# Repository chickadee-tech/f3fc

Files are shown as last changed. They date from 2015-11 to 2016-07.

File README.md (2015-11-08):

# Chickadee Tech F3FC #
This an STM32F3-based flight control Polystack board for multirotors designed by Chickadee Tech. It features an STM32F303VCT6 microcontroller and an MPU-6000 accelerometer/gyroscope. It runs a modified version of [Betaflight]() available [here](github.com/chickadee-tech/betaflight) with the CKD_F3FC target.

## Documentation ##
See the [wiki](https://github.com/chickadee-tech/f3fc/wiki) for documentation.

## Polystack ##
This **control** board is part of the Polystack platform for modular microcontrol systems. More information on the platform can be found at [polystack.org](http://polystack.org).

## Support ##
If you need support with a board you own or have development questions please email support@chickadee.tech or check chickadee.tech/support for other ways to get support.

## Support ##
If you need support with a board you own or have development questions please email support@chickadee.tech or check [chickadee.tech/support](https://chickadee.tech/support) for other ways to get support.

## Contributing ##
Please note that this project is released with a [Contributor Code of Conduct](CODE_OF_CONDUCT.md). By participating in this project you agree to abide by its terms.

### Setup ###
Components and footprints for PCB parts are not included in this repository. Instead, checkout the [chickadee-tech/kicad-libs](https://github.com/chickadee-tech/kicad-libs) repository in the same directory that this repository is checked out in. All part definitions should be relative so that they will load correctly.

### Pull requests ###
For fixes please submit a pull request to the original repository. After the pull request is merged, check the [Chickadee Tech Active Contributor Discount (ACD)](https://chickadee.tech/active-contributor) to see if you are eligible for a discount code to use on your next purchase.

### Derivatives ###
If developing your own version of the F3FC board please remove all Chickadee Tech trademarks and follow the [CC-BY license](LICENSE). While not required, please consider open sourcing your modifications so others can learn from your improvements. If you do email support@chickadee.tech and we may choose to add your project to the ACD.

You may also license the Polystack logo for free by emailing support@chickadee.tech. We'll ask for your gerbers to ensure the design complies with specifications laid out [here](https://github.com/chickadee-tech/polystack/wiki) and provide written permission to use the trademark after compliance has been demonstrated.

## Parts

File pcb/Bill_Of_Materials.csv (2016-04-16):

part name | symbol | size (imp) | max current | unit price | units per build | units in stock | On Order | order total | Manufacturer ID | digikey url | Mouser | MacroFab HP | datasheet | datasheet2
C 10nF (0.01uF, 10000pF) X7R | C5 | 603 |  | $0.01 | 1 | 96 | SMD Binder - Capacitors | $0.01 | 06035C103KAT2A | http://www.digikey.com/product-detail/en/06035C103KAT2A/478-1227-1-ND/564259 |  | Y | http://datasheets.avx.com/X7RDielectric.pdf
C 10uF X5R | C11 | 1206 |  | $0.24 | 1 | 80 | SMD Binder - Capacitors | $0.24 | C3216X5R1C106M160AA | http://www.digikey.com/product-detail/en/C3216X5R1C106M160AA/445-1426-1-ND/569092 |  | MF-CAP-1206-10uF | http://product.tdk.com/en/catalog/datasheets/mlcc_commercial_general_en.pdf
C 1uF X7R | C12 | 603 |  | $0.03 | 1 | 20 | SMD Binder - Capacitors | $0.03 | TMK107B7105KA-T | http://www.digikey.com/product-detail/en/TMK107B7105KA-T/587-2984-1-ND/2714177 |  | MF-CAP-0603-1uF | http://ds.yuden.co.jp/TYCOMPAS/ut/detail.do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
C 2.2nF (2200pF) X7R 50V | C1 | 603 |  | $0.01 | 1 | 94 | SMD Binder - Capacitors | $0.01 | C0603C222K5RACTU | http://www.digikey.com/product-detail/en/C0603C222K5RACTU/399-1085-1-ND/411360 | http://www.mouser.com/ProductDetail/Kemet/C0603C222K5RACTU/?qs=sGAEpiMZZMs0AnBnWHyRQFqPnX0OlvcoEeor2YsHDUE%3d | N
C 2.2uF | C14, C15 | 603 |  | $0.05 | 2 | 92 | SMD Binder - Capacitors | $0.09 | C0603C225K9PACTU | http://www.digikey.com/product-detail/en/C0603C225K9PACTU/399-3362-1-ND/650351 | http://www.mouser.com/ProductDetail/Kemet/C0603C225K9PACTU/?qs=sGAEpiMZZMs0AnBnWHyRQJIiGvDVk92V8FIBbbmgLZk%3d
C 0.1uF | C2, C3, C7, C8, C9, C10, C13 | 603 |  | $0.02 | 7 | 400 | SMD Binder - Capacitors | $0.15 | C0603C104K4RACTU | http://www.digikey.com/product-detail/en/C0603C104K4RACTU/399-1096-1-ND/411371 |  | MF-CAP-0603-0.1uF | http://www.kemet.com/docfinder?Partnumber=C0603C104K4RACTU
red led | D3,D5 |  |  | $0.19 | 2 | 71 | SMD Binder - Diodes | $0.37 | LTST-C190KRKT | http://www.digikey.com/product-detail/en/LTST-C190KRKT/160-1436-1-ND/386816 |  | MF-LED-0603-RED | http://optoelectronics.liteon.com/upload/download/DS-22-99-0151/S_110_LTST-C190KRKT.pdf
green led | D1 |  |  | $0.19 | 1 | 83 | SMD Binder - Diodes | $0.19 | LTST-C190KGKT | http://www.digikey.com/product-detail/en/LTST-C190KGKT/160-1435-1-ND/386814 |  | Y | http://optoelectronics.liteon.com/upload/download/DS22-2000-074/S_110_LTST-C190KGKT.pdf
yellow led | D2 |  |  | $0.20 | 1 | 87 | SMD Binder - Diodes | $0.20 | LTST-C190KSKT | http://www.digikey.com/product-detail/en/LTST-C190KSKT/160-1437-1-ND/386818 |  | N | http://optoelectronics.liteon.com/upload/download/DS-22-99-0189/S_110_LTST-C190KSKT.pdf
Power OR Diode | D4 |  | 500mA | $0.49 | 1 | 6 | SMD Binder - Diodes | $0.49 | PMEG2005CT,215 | http://www.digikey.com/product-detail/en/PMEG2005CT,215/568-6500-1-ND/2531787 | http://www.mouser.com/ProductDetail/NXP/PMEG2005CT215/ | N | http://www.nxp.com/documents/data_sheet/PMEG2005CT.pdf
~3.5mm Spacer | Off Board |  |  | $0.08 | 5 | 81 | SMD Binder - Connectors | $0.42 | 908-140 | http://www.mouser.com/search/ProductDetail.aspx?R=0virtualkey0virtualkey908-140 |  | N
Nylon Hex Nut | Off Board |  |  | $0.10 | 9 | 94 | SMD Binder - Connectors | $0.86 | 4688 | http://www.mouser.com/ProductDetail/Keystone-Electronics/4688/ |  | N
1x2 housing | Off Board |  |  | $0.08 | 4 | 48 | SMD Binder - Connectors | $0.31 | M20-1060200 | http://www.digikey.com/product-detail/en/M20-1060200/952-2227-ND/3728191 | http://www.mouser.com/ProductDetail/Harwin/M20-1060200/ | N
usb otg | P2 |  | 500mA | $0.46 | 1 | 7 | SMD Binder - Connectors | $0.46 | 10118193-0001LF | http://www.digikey.com/product-detail/en/10118193-0001LF/609-4616-1-ND/2785380 | http://www.mouser.com/ProductDetail/FCI/10118193-0001LF/ | MF-CON-MICROUSB-RIGHT | http://portal.fciconnect.com/Comergent//fci/drawing/10118193.pdf
80 pin receptacle (3.5mm) | P4 |  | 0.3A a pin | $2.42 | 1 | 1 | SMD Binder - Connectors | $2.42 | DF40HC(3.5)-80DS-0.4V(51) | http://www.digikey.com/product-detail/en/DF40HC(3.5)-80DS-0.4V(51)/H11997CT-ND/2880228 | http://www.mouser.com/ProductDetail/Hirose-Electric/DF40HC35-80DS-04V51/ | N | http://www.hirose.co.jp/cataloge_hp/ed_DF40_20140305.pdf
20pin hirose header | P5 |  | 0.3A a pin | $0.79 | 1 | 7 | SMD Binder - Connectors | $0.79 | DF40C-20DP-0.4V(51) | http://www.digikey.com/product-detail/en/DF40C-20DP-0.4V(51)/H11618CT-ND/1969498 | http://www.mouser.com/ProductDetail/Hirose-Electric/DF40C-20DP-04V51/ | N | http://www.hirose.co.jp/cataloge_hp/ed_DF40_20140305.pdf
Chickadee F3FC v7 | PCB |  |  | $6.73 | 1 | 3 |  | $6.73 | CKD-F3FC-V7 |  |  | N
p-channel mosfet | Q1 | TO-236-3, SC-59, SOT-23-4 | 220mA continuous | $0.10 | 1 | 97 | SMD Binder - ICs | $0.10 | BSS84 | http://www.digikey.com/product-detail/en/fairchild-semiconductor/BSS84/BSS84CT-ND/244297 | http://www.mouser.com/search/ProductDetail.aspx?R=0virtualkey0virtualkeyBSS84 | MF-DSC-SOT233-BSS84 | https://www.fairchildsemi.com/datasheets/BS/BSS84.pdf
n-channel mosfet | Q3, Q4 | TO-236-3, SC-59, SOT-23-3 | 220mA continuous | $0.09 | 2 | 59 | SMD Binder - ICs | $0.19 | BSS138 | http://www.digikey.com/product-detail/en/BSS138/BSS138CT-ND/244294 |  | MF-DSC-SOT233-BSS138 | https://www.fairchildsemi.com/datasheets/BS/BSS138.pdf
R 1k | R1, R2, R3, R12 | 603 |  | $0.01 | 4 | 993 | SMD Binder - Resistors | $0.04 | RC0603FR-071KL | http://www.digikey.com/product-detail/en/RC0603FR-071KL/311-1.00KHRCT-ND/729790 |  | MF-RES-0603-1K | http://www.yageo.com/NewPortal/yageodocoutput?fileName=/pdf/R-Chip/PYu-RC_Group_51_RoHS_L_3.pdf
R 4.7k | R4, R11 | 1206 |  | $0.01 | 2 | 68 | SMD Binder - Resistors | $0.01 | RC0603FR-074K7L | http://www.digikey.com/product-detail/en/RC0603FR-074K7L/311-4.70KHRCT-ND/730159 |  | MF-RES-0603-5.6K | http://www.yageo.com/NewPortal/yageodocoutput?fileName=/pdf/R-Chip/PYu-RC_Group_51_RoHS_L_3.pdf
R 10k | R5, R7 | 603 |  | $0.01 | 2 | 979 | SMD Binder - Resistors | $0.02 | RC0603FR-0710KL | http://www.digikey.com/product-detail/en/RC0603FR-0710KL/311-10.0KHRCT-ND/729827 |  | MF-RES-0603-10K | http://www.yageo.com/NewPortal/yageodocoutput?fileName=/pdf/R-Chip/PYu-RC_Group_51_RoHS_L_3.pdf
R 1.5k | R6 | 603 |  | $0.01 | 1 | 0 |  | $0.01 | RC0603FR-071K5L | http://www.digikey.com/product-detail/en/yageo/RC0603FR-071K5L/311-1.50KHRCT-ND/729811 |  | N
R 100k | R10 | 603 |  | $0.01 | 1 | 55 | SMD Binder - Resistors | $0.01 | RC0603FR-07100KL | http://www.digikey.com/product-detail/en/RC0603FR-07100KL/311-100KHRCT-ND/729836 |  | MF-RES-0603-100K | http://www.yageo.com/NewPortal/yageodocoutput?fileName=/pdf/R-Chip/PYu-RC_Group_51_RoHS_L_3.pdf
R 470k | R9 | 603 |  | $0.01 | 1 | 68 | SMD Binder - Resistors | $0.01 | RC0603FR-07470KL | http://www.digikey.com/product-detail/en/RC0603FR-07470KL/311-470KHRCT-ND/730204 |  | MF-RES-0603-470K | http://www.yageo.com/NewPortal/yageodocoutput?fileName=/pdf/R-Chip/PYu-RC_Group_51_RoHS_L_3.pdf
reset- side switch | SW1 | EVQ-P7A |  | $0.69 | 1 | 7 | SMD Binder - Misc | $0.69 | EVQ-P7A01P | http://www.digikey.com/product-detail/en/EVQ-P7A01P/P16763CT-ND/4429456 | http://www.mouser.com/ProductDetail/Panasonic/EVQ-P7A01P/ | N | http://media.digikey.com/pdf/Data%20Sheets/Panasonic%20Electronic%20Components/EVQP(7,3,9P7).pdf
acc/gyro | U1 | 24pin QFN 4x4 |  | $10.72 | 1 | 4 | SMD Binder - ICs | $10.72 | MPU-6000 | http://www.digikey.com/product-detail/en/MPU-6000/1428-1005-1-ND/4038006 |  | N | http://store.invensense.com/datasheets/invensense/MPU-6050_DataSheet_V3%204.pdf
STM32F303 | U2 | LQFP-100 | 160mA | $8.66 | 1 | 3 | SMD Binder - ICs | $8.66 | STM32F303VCT6- | http://www.digikey.com/product-detail/en/STM32F303VCT6/497-13233-ND/3598127 | http://www.mouser.com/ProductDetail/STMicroelectronics/STM32F303VCT6/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 | N | http://www.st.com/st-web-ui/static/active/en/resource/technical/document/datasheet/DM00058181.pdf | Total Price | $36.32
3.3v regulator | U3 | SOT23-5 | 0.3A | $0.49 | 1 | 8 | SMD Binder - ICs | $0.49 | TLV70233DBVR | http://www.digikey.com/product-detail/en/TLV70233DBVR/296-32415-1-ND/3505572 | http://www.mouser.com/ProductDetail/Texas-Instruments/TLV70233DBVR/?qs=sGAEpiMZZMu%2feW%252ba9Wiy7YTpE8hEJFai | MF-REG-SOT235-3.3V-300mA | http://www.ti.com/lit/ds/symlink/tlv702.pdf
8mhz resonator | X1 |  |  | $0.38 | 1 | 8 | SMD Binder - Misc | $0.38 | CSTCE8M00G55-R0 | https://www.digikey.com/product-detail/en/CSTCE8M00G55-R0/490-1195-1-ND/584632 | http://www.mouser.com/ProductDetail/Murata/CSTCE8M00G55-R0/ | N | http://www.murata.com/~/media/webrenewal/support/library/catalog/products/timingdevice/ceralock/p16e.ashx
2x4 right angle | Off Board |  |  | $0.80 | 1 | 2 | SMD Binder - Connectors | $0.80 | 5-102975-4 |  | http://www.mouser.com/ProductDetail/TE-Connectivity-AMP/5-102975-4/ | N
~2mm Spacer | Off Board |  |  | $0.08 | 5 | 100 | SMD Binder - Connectors | $0.42 | 908-080 | http://www.mouser.com/ProductDetail/Bivar/908-080/?qs=sGAEpiMZZMtU66%252bVMtdfbpPy1E%252bha670 |  | N | http://www.bivar.com/Portals/0/Products/d.ashx?f=/Portals/0/products/9XX-XXX.pdf

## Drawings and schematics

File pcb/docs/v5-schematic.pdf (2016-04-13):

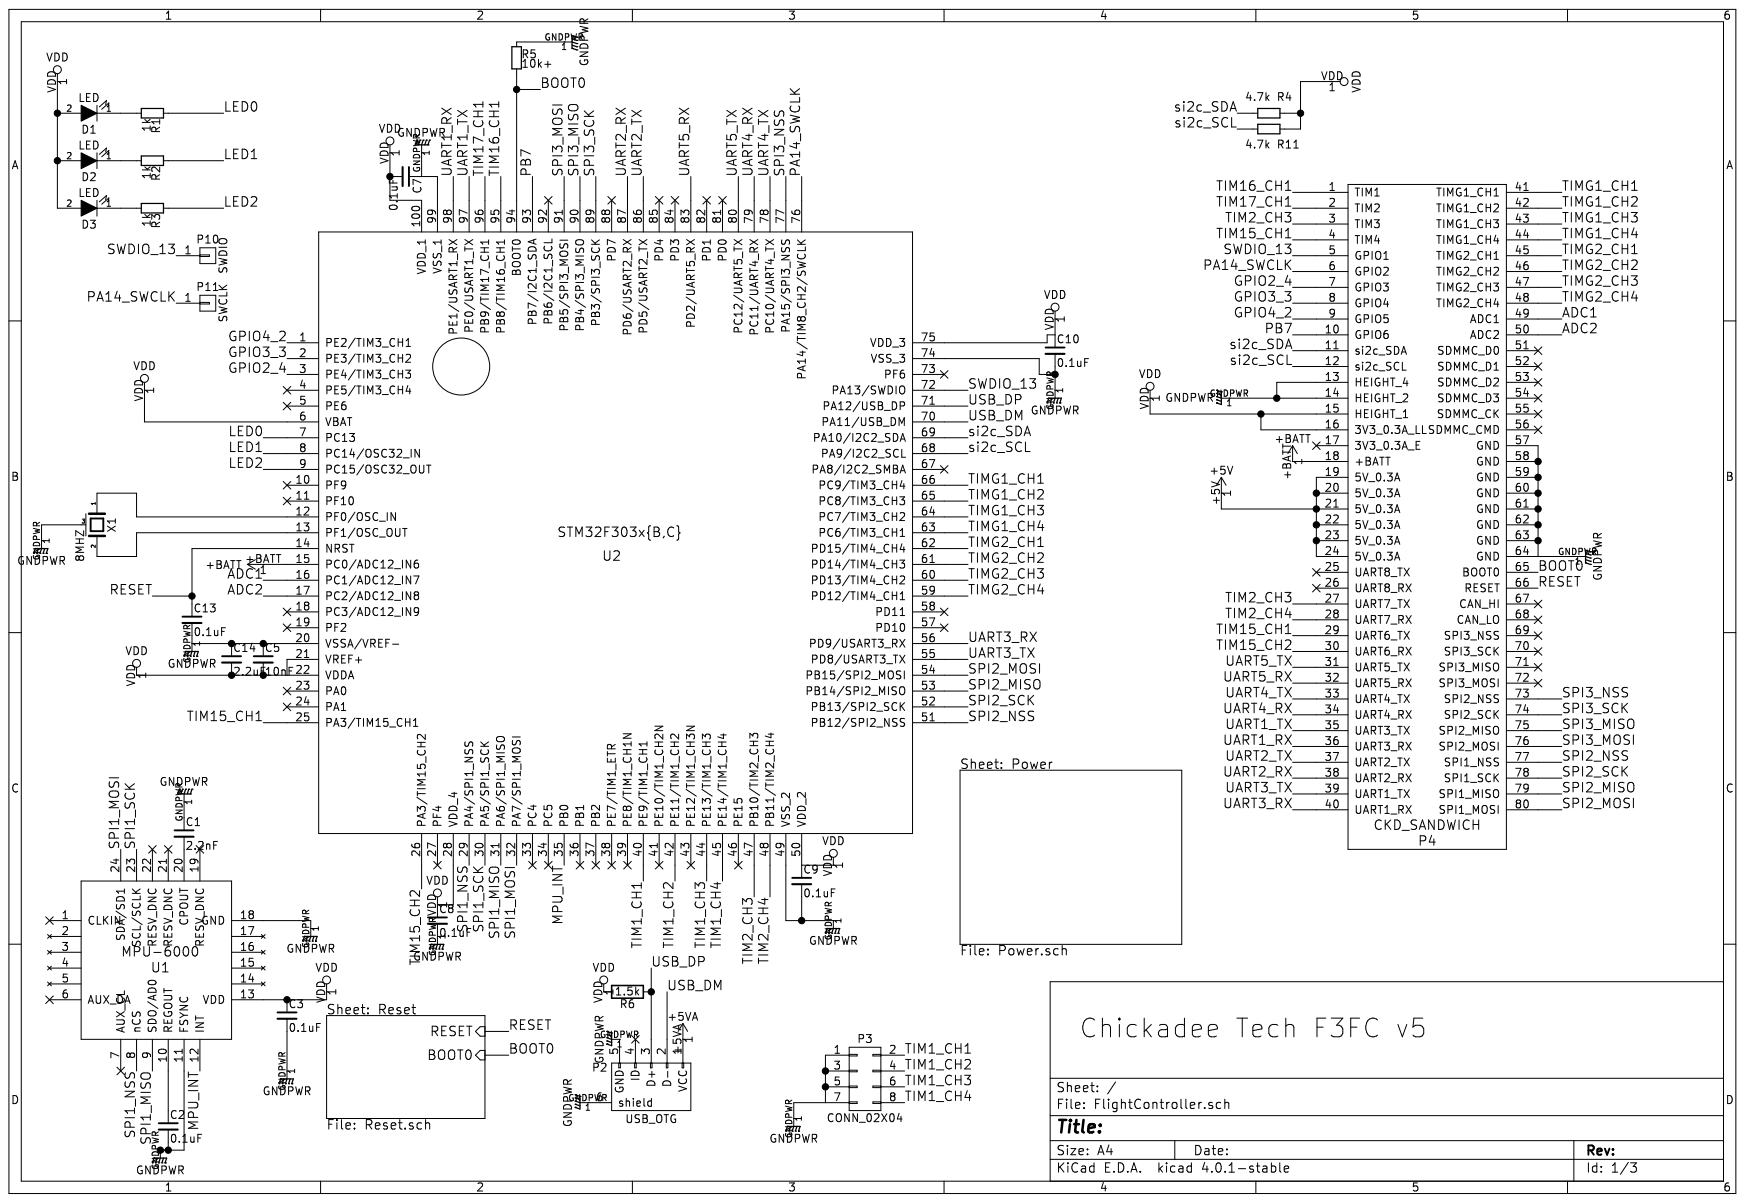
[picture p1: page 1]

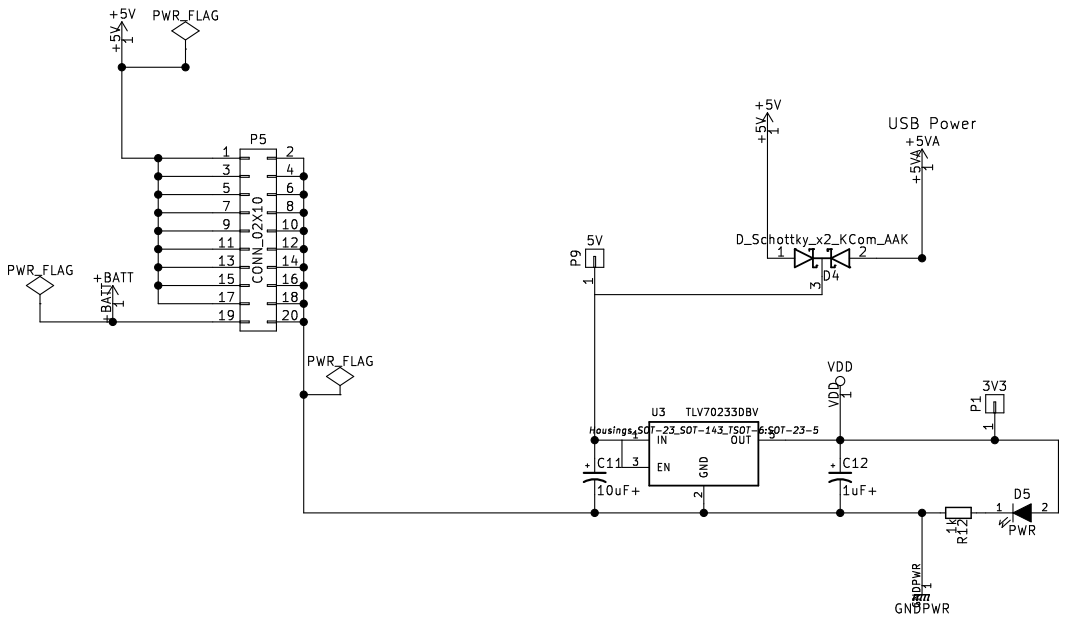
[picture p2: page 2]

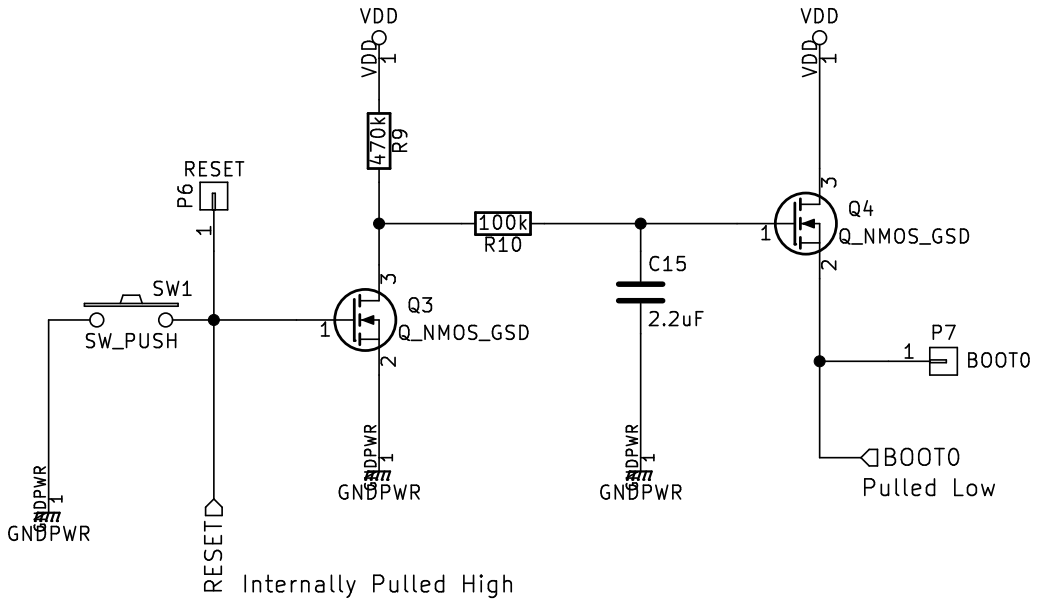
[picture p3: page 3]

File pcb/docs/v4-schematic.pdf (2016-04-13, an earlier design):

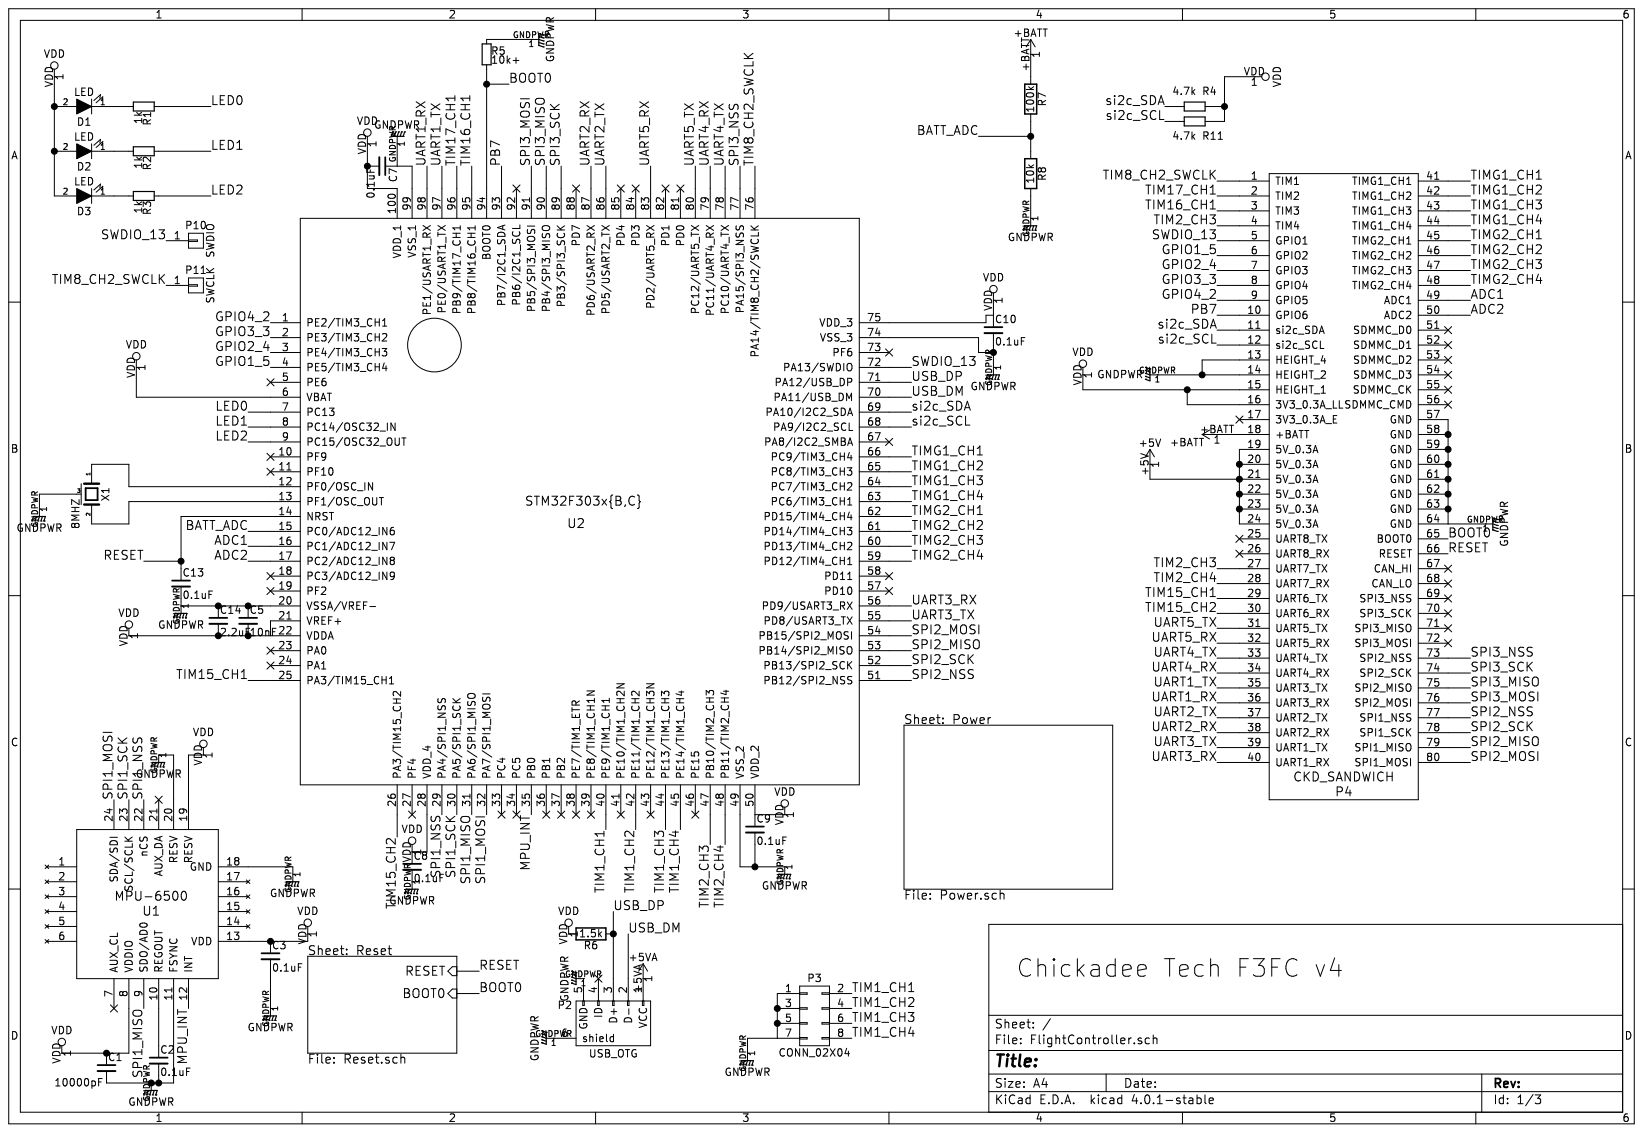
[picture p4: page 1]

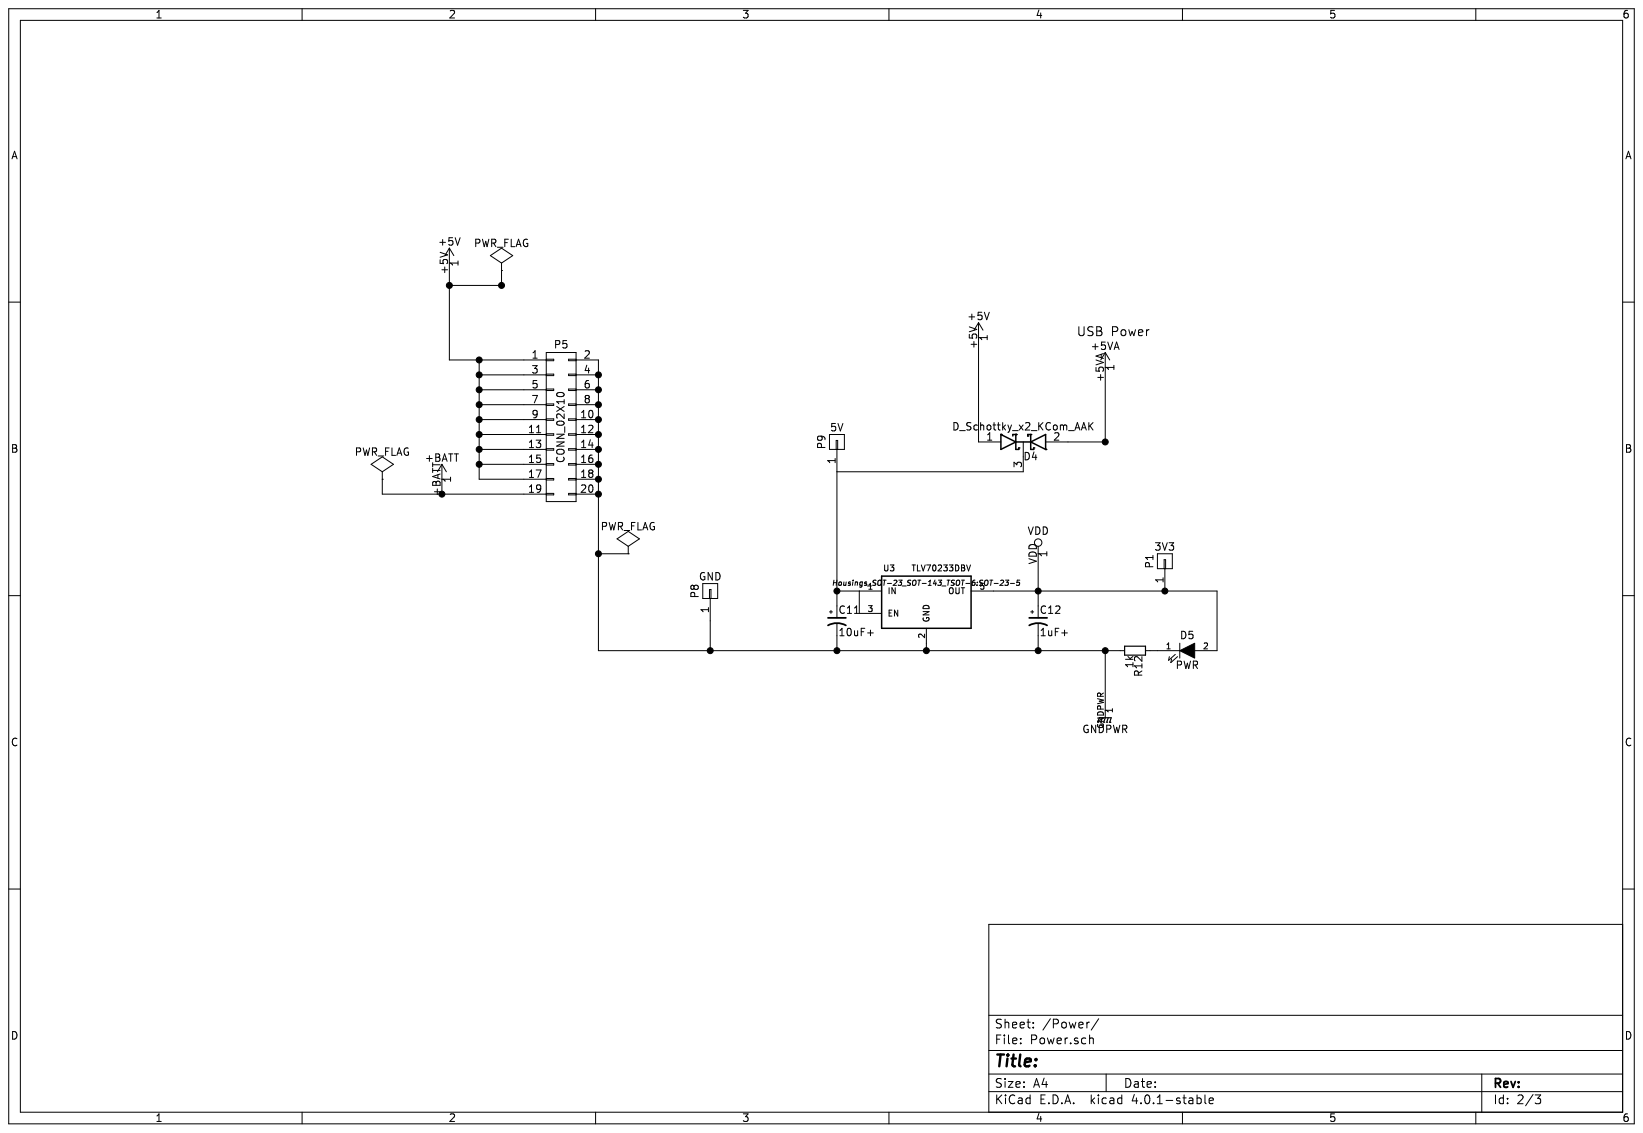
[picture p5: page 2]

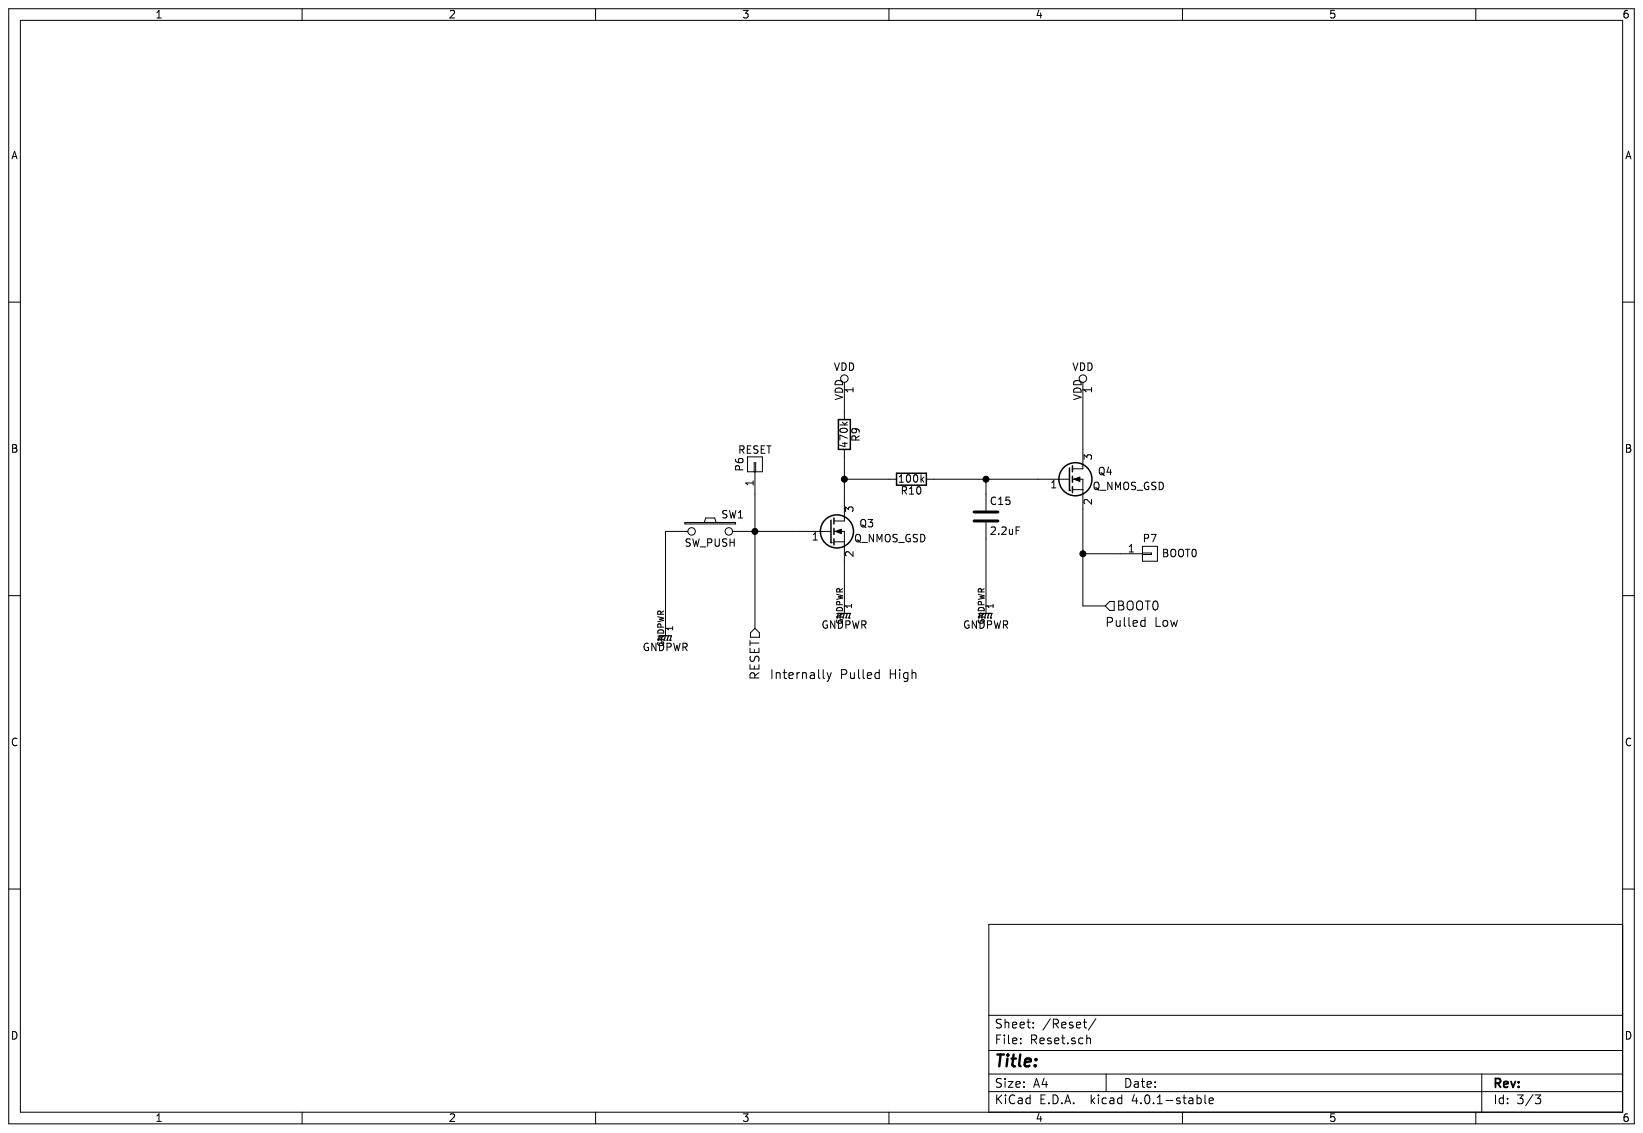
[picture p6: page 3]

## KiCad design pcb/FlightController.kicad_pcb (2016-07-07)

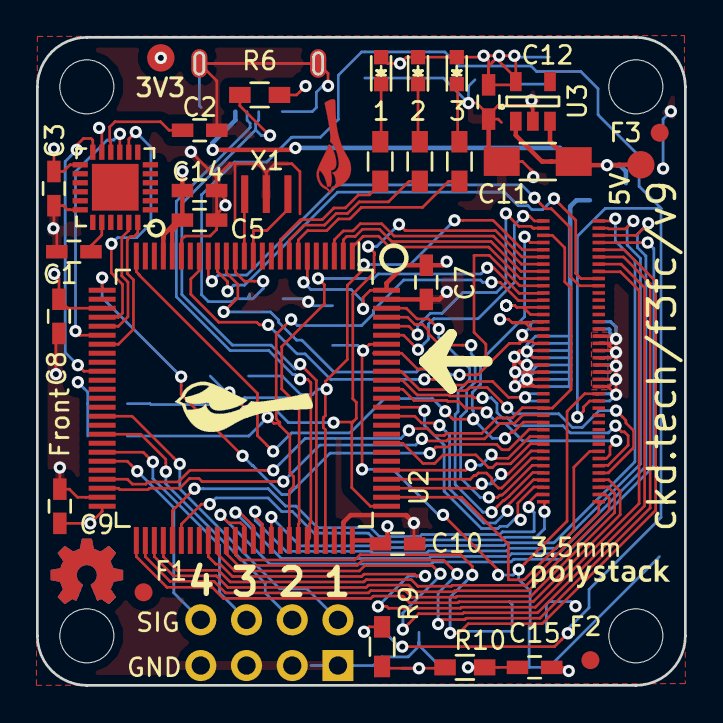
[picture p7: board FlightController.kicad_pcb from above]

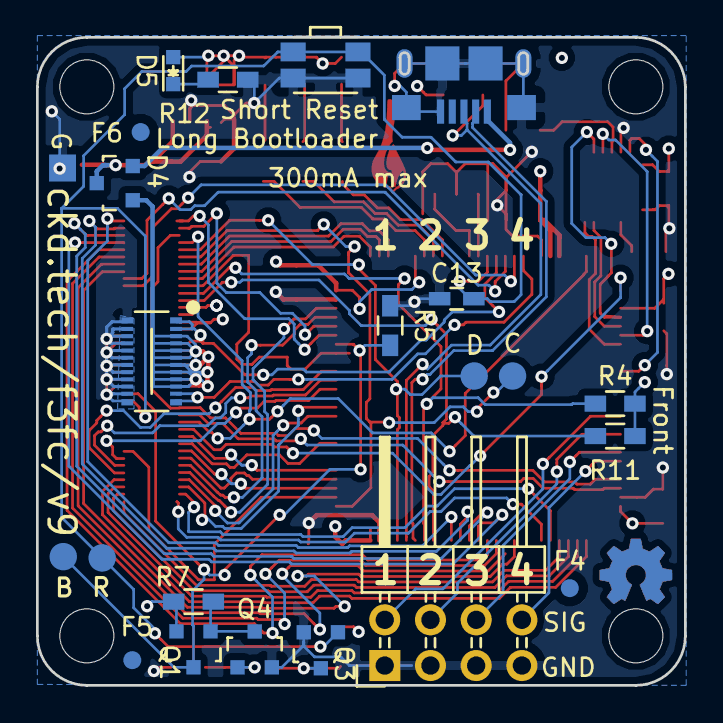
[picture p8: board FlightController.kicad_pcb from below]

Board: 4 copper layers, 36.0 x 36.0 mm, 55 parts (23 on the bottom side), 76 nets.

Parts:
C1: 2.2nF; C_0603_HandSoldering
C2, C3, C7, C8, C9, C10, C13: 0.1uF; C_0603_HandSoldering
C5: 10nF; C_0603_HandSoldering
C11: 10uF+; C_1206_HandSoldering
C12: 1uF+; C_0603_HandSoldering
C14, C15: 2.2uF; C_0603_HandSoldering
D1: Green; LED-0603
D2: Yellow; LED-0603
D3, D5: Red; LED-0603
D4: D_Schottky_x2_KCom_AAK; SOT-23
F1, F2, F3, F4, F5, F6: 1mm; Fiducial
P1: 3V3; Measurement_Point_Round-SMD-Pad_Small
P2: USB_OTG; Mini-USB-B-EDGE
P3: CONN_02X04; Pin_Header_Angled_2x04
P4: CKD_SANDWICH; DF40-3-4mm-80pin-Receptacle
P5: CONN_02X10; DF40-20pin-Header
P6: RESET; Measurement_Point_Round-SMD-Pad_Small
P7: BOOT0; Measurement_Point_Round-SMD-Pad_Small
P8: CONN_01X01; Measurement_Point_Square-SMD-Pad_Small
P9: 5V; Measurement_Point_Round-SMD-Pad_Small
P10: SWDIO; Measurement_Point_Round-SMD-Pad_Small
P11: SWCLK; Measurement_Point_Round-SMD-Pad_Small
Q1: Q_PMOS_GSD; SOT-23
Q3, Q4: Q_NMOS_GSD; SOT-23
R1, R2, R3, R12: 1k; R_0603_HandSoldering
R4, R11: 4.7k; R_0603_HandSoldering
R5: 10k+; R_0603_HandSoldering
R6: 1.5k; R_0603_HandSoldering
R7: 10k; R_0603_HandSoldering
R9: 470k; R_0603_HandSoldering
R10: 100k; R_0603_HandSoldering
SW1: SW_PUSH; SW_SPST_EVQP7A
U1: MPU-6000; QFN-24-1EP_4x4mm_Pitch0.5mm
U2: STM32F303x{B,C}; LQFP-100_14x14mm_Pitch0.5mm
U3: TLV70233DBV; SOT-23-5
X1: 8MHZ; CSTCE_G-CSTCE_G_Z
svg2mod: G***; polystack-bold-0.4

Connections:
+5V: D4.1, P4.19, P4.20, P4.21, P4.22, P4.23, P4.24, P5.3, P5.5, P5.7, P5.9, P5.11, P5.13, P5.15, P5.17
+5VA: D4.2, P2.1
+BATT: P4.18, P5.19, U2.15
/ADC1: P4.49, U2.16
/ADC2: P4.50, U2.17
/GPIO2_4: P4.7, U2.3
/GPIO3_3: P4.8, U2.2
/GPIO4_2: P4.9, U2.1
/LED0: R3.1, U2.7
/LED1: R2.1, U2.8
/LED2: R1.1, U2.9
/MPU_INT: U1.12, U2.35
/PA14_SWCLK: P4.6, P11.1, U2.76
/PB7: P4.10, U2.93
/Power/CURRENT: P5.1, U2.18
/Reset/BOOT0: P4.65, P7.1, Q1.3, R5.2, U2.94
/Reset/RESET: C13.1, P4.66, P6.1, Q3.1, SW1.2, U2.14
/SPI1_MISO: U1.9, U2.31
/SPI1_MOSI: U1.24, U2.32
/SPI1_NSS: U1.8, U2.29
/SPI1_SCK: U1.23, U2.30
/SPI2_MISO: P4.79, U2.53
/SPI2_MOSI: P4.80, U2.54
/SPI2_NSS: P4.77, U2.51
/SPI2_SCK: P4.78, U2.52
/SPI3_MISO: P4.75, U2.90
/SPI3_MOSI: P4.76, U2.91
/SPI3_NSS: P4.73, U2.77
/SPI3_SCK: P4.74, U2.89
/SWDIO_13: P4.5, P10.1, U2.72
/TIM1_CH1: P3.2, U2.40
/TIM1_CH2: P3.4, U2.42
/TIM1_CH3: P3.6, U2.44
/TIM1_CH4: P3.8, U2.45
/TIM2_CH3: P4.3, P4.27, U2.47
/TIM2_CH4: P4.28, U2.48
/TIM15_CH1: P4.4, P4.29, U2.25
/TIM15_CH2: P4.30, U2.26
/TIM16_CH1: P4.1, U2.95
/TIM17_CH1: P4.2, U2.96
/TIMG1_CH1: P4.41, U2.66
/TIMG1_CH2: P4.42, U2.65
/TIMG1_CH3: P4.43, U2.64
/TIMG1_CH4: P4.44, U2.63
/TIMG2_CH1: P4.45, U2.62
/TIMG2_CH2: P4.46, U2.61
/TIMG2_CH3: P4.47, U2.60
/TIMG2_CH4: P4.48, U2.59
/UART1_RX: P4.36, U2.98
/UART1_TX: P4.35, U2.97
/UART2_RX: P4.38, U2.87
/UART2_TX: P4.37, U2.86
/UART3_RX: P4.40, U2.56
/UART3_TX: P4.39, U2.55
/UART4_RX: P4.34, U2.79
/UART4_TX: P4.33, U2.78
/UART5_RX: P4.32, U2.83
/UART5_TX: P4.31, U2.80
/USB_D+: P2.3, R6.1, U2.71
/USB_D-: P2.2, U2.70
/si2c_SCL: P4.12, R11.2, U2.68
/si2c_SDA: P4.11, R4.2, U2.69
GNDPWR: C1.1, C2.2, C3.2, C5.1, C7.1, C8.2, C9.2, C10.2, C11.2, C12.2, C13.2, C14.1, C15.2, P2.5, P2.6, P3.1, P3.3, P3.5, P3.7, P4.13, P4.14, P4.57, P4.58, P4.59, P4.60, P4.61, P4.62, P4.63, P4.64, P5.2, P5.4, P5.6, P5.8, P5.10, P5.12, P5.14, P5.16, P5.18, P5.20, P8.1, Q3.2, Q4.2, R5.1, R12.2, SW1.1, U1.11, U1.18, U2.20, U2.49, U2.74, U2.99, U3.2, X1.3
unnamed: C1.2, U1.20
unnamed: C2.1, U1.10
unnamed: C11.1, D4.3, P9.1, U3.1, U3.3
unnamed: C15.1, Q4.1, R10.1
unnamed: D1.1, R1.2
unnamed: D2.1, R2.2
unnamed: D3.1, R3.2
unnamed: D5.1, R12.1
unnamed: Q1.1, Q4.3, R7.2
unnamed: Q3.3, R9.2, R10.2
unnamed: U2.12, X1.1
unnamed: U2.13, X1.2
VDD: C3.1, C5.2, C7.2, C8.1, C9.1, C10.1, C12.1, C14.2, D1.2, D2.2, D3.2, D5.2, P1.1, P4.15, P4.16, Q1.2, R4.1, R6.2, R7.1, R9.1, R11.1, U1.13, U2.6, U2.21, U2.22, U2.28, U2.50, U2.75, U2.100, U3.5

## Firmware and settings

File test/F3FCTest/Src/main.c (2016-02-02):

/**
  ******************************************************************************
  * File Name          : main.c
  * Description        : Main program body
  ******************************************************************************
  *
  * COPYRIGHT(c) 2015 STMicroelectronics
  *
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
  ******************************************************************************
  */
/* Includes ------------------------------------------------------------------*/
#include "stm32f3xx_hal.h"

UART_HandleTypeDef huart4;
UART_HandleTypeDef huart5;
UART_HandleTypeDef huart2;
UART_HandleTypeDef huart3;

PCD_HandleTypeDef hpcd_USB_FS;

/* USER CODE BEGIN PV */

/* USER CODE END PV */

void SystemClock_Config(void);
static void MX_GPIO_Init(void);
static void MX_UART4_Init(void);
static void MX_UART5_Init(void);
static void MX_USART2_UART_Init(void);
static void MX_USART3_UART_Init(void);
static void MX_USB_PCD_Init(void);

/* USER CODE BEGIN PFP */

/* USER CODE END PFP */

int main(void)
{

  /* MCU Configuration----------------------------------------------------------*/

  /* Reset of all peripherals, Initializes the Flash interface and the Systick. */
  HAL_Init();

  /* Configure the system clock */
  SystemClock_Config();

  /* Initialize all configured peripherals */
  MX_GPIO_Init();
  MX_UART4_Init();
  MX_UART5_Init();
  MX_USART2_UART_Init();
  MX_USART3_UART_Init();
  MX_USB_PCD_Init();

  /* USER CODE BEGIN 2 */
  long i = 0;
  /* USER CODE END 2 */

  /* Infinite loop */
  /* USER CODE BEGIN WHILE */
  while (1)
  {
    HAL_GPIO_TogglePin(GPIOC, GPIO_PIN_13);
    HAL_GPIO_TogglePin(GPIOC, GPIO_PIN_14);
    HAL_GPIO_TogglePin(GPIOC, GPIO_PIN_15);
    for(i = 0; i < 50000; i++);
  /* USER CODE END WHILE */

  /* USER CODE BEGIN 3 */

  }
  /* USER CODE END 3 */

}

/** System Clock Configuration
*/
void SystemClock_Config(void)
{

  RCC_OscInitTypeDef RCC_OscInitStruct;
  RCC_ClkInitTypeDef RCC_ClkInitStruct;
  RCC_PeriphCLKInitTypeDef PeriphClkInit;

  RCC_OscInitStruct.OscillatorType = RCC_OSCILLATORTYPE_HSE;
  RCC_OscInitStruct.HSEState = RCC_HSE_ON;
  RCC_OscInitStruct.HSEPredivValue = RCC_HSE_PREDIV_DIV1;
  RCC_OscInitStruct.PLL.PLLState = RCC_PLL_ON;
  RCC_OscInitStruct.PLL.PLLSource = RCC_PLLSOURCE_HSE;
  RCC_OscInitStruct.PLL.PLLMUL = RCC_PLL_MUL9;
  HAL_RCC_OscConfig(&RCC_OscInitStruct);

  RCC_ClkInitStruct.ClockType = RCC_CLOCKTYPE_SYSCLK|RCC_CLOCKTYPE_PCLK1;
  RCC_ClkInitStruct.SYSCLKSource = RCC_SYSCLKSOURCE_PLLCLK;
  RCC_ClkInitStruct.AHBCLKDivider = RCC_SYSCLK_DIV1;
  RCC_ClkInitStruct.APB1CLKDivider = RCC_HCLK_DIV2;
  RCC_ClkInitStruct.APB2CLKDivider = RCC_HCLK_DIV1;
  HAL_RCC_ClockConfig(&RCC_ClkInitStruct, FLASH_LATENCY_2);

  PeriphClkInit.PeriphClockSelection = RCC_PERIPHCLK_USB|RCC_PERIPHCLK_USART2
                              |RCC_PERIPHCLK_USART3|RCC_PERIPHCLK_UART4
                              |RCC_PERIPHCLK_UART5;
  PeriphClkInit.Usart2ClockSelection = RCC_USART2CLKSOURCE_PCLK1;
  PeriphClkInit.Usart3ClockSelection = RCC_USART3CLKSOURCE_PCLK1;
  PeriphClkInit.Uart4ClockSelection = RCC_UART4CLKSOURCE_PCLK1;
  PeriphClkInit.Uart5ClockSelection = RCC_UART5CLKSOURCE_PCLK1;
  PeriphClkInit.USBClockSelection = RCC_USBPLLCLK_DIV1_5;
  HAL_RCCEx_PeriphCLKConfig(&PeriphClkInit);

  HAL_SYSTICK_Config(HAL_RCC_GetHCLKFreq()/1000);

  HAL_SYSTICK_CLKSourceConfig(SYSTICK_CLKSOURCE_HCLK);

  /* SysTick_IRQn interrupt configuration */
  HAL_NVIC_SetPriority(SysTick_IRQn, 0, 0);
}

/* UART4 init function */
void MX_UART4_Init(void)
{

  huart4.Instance = UART4;
  huart4.Init.BaudRate = 115200;
  huart4.Init.WordLength = UART_WORDLENGTH_8B;
  huart4.Init.StopBits = UART_STOPBITS_1;
  huart4.Init.Parity = UART_PARITY_NONE;
  huart4.Init.Mode = UART_MODE_TX_RX;
  huart4.Init.HwFlowCtl = UART_HWCONTROL_NONE;
  huart4.Init.OverSampling = UART_OVERSAMPLING_16;
  huart4.Init.OneBitSampling = UART_ONEBIT_SAMPLING_DISABLED ;
  huart4.AdvancedInit.AdvFeatureInit = UART_ADVFEATURE_NO_INIT;
  HAL_UART_Init(&huart4);

}

/* UART5 init function */
void MX_UART5_Init(void)
{

  huart5.Instance = UART5;
  huart5.Init.BaudRate = 115200;
  huart5.Init.WordLength = UART_WORDLENGTH_8B;
  huart5.Init.StopBits = UART_STOPBITS_1;
  huart5.Init.Parity = UART_PARITY_NONE;
  huart5.Init.Mode = UART_MODE_TX_RX;
  huart5.Init.HwFlowCtl = UART_HWCONTROL_NONE;
  huart5.Init.OverSampling = UART_OVERSAMPLING_16;
  huart5.Init.OneBitSampling = UART_ONEBIT_SAMPLING_DISABLED ;
  huart5.AdvancedInit.AdvFeatureInit = UART_ADVFEATURE_NO_INIT;
  HAL_UART_Init(&huart5);

}

/* USART2 init function */
void MX_USART2_UART_Init(void)
{

  huart2.Instance = USART2;
  huart2.Init.BaudRate = 38400;
  huart2.Init.WordLength = UART_WORDLENGTH_8B;
  huart2.Init.StopBits = UART_STOPBITS_1;
  huart2.Init.Parity = UART_PARITY_NONE;
  huart2.Init.Mode = UART_MODE_TX_RX;
  huart2.Init.HwFlowCtl = UART_HWCONTROL_NONE;
  huart2.Init.OverSampling = UART_OVERSAMPLING_16;
  huart2.Init.OneBitSampling = UART_ONEBIT_SAMPLING_DISABLED ;
  huart2.AdvancedInit.AdvFeatureInit = UART_ADVFEATURE_NO_INIT;
  HAL_UART_Init(&huart2);

}

/* USART3 init function */
void MX_USART3_UART_Init(void)
{

  huart3.Instance = USART3;
  huart3.Init.BaudRate = 38400;
  huart3.Init.WordLength = UART_WORDLENGTH_8B;
  huart3.Init.StopBits = UART_STOPBITS_1;
  huart3.Init.Parity = UART_PARITY_NONE;
  huart3.Init.Mode = UART_MODE_TX_RX;
  huart3.Init.HwFlowCtl = UART_HWCONTROL_NONE;
  huart3.Init.OverSampling = UART_OVERSAMPLING_16;
  huart3.Init.OneBitSampling = UART_ONEBIT_SAMPLING_DISABLED ;
  huart3.AdvancedInit.AdvFeatureInit = UART_ADVFEATURE_NO_INIT;
  HAL_UART_Init(&huart3);

}

/* USB init function */
void MX_USB_PCD_Init(void)
{

  hpcd_USB_FS.Instance = USB;
  hpcd_USB_FS.Init.dev_endpoints = 8;
  hpcd_USB_FS.Init.speed = PCD_SPEED_FULL;
  hpcd_USB_FS.Init.ep0_mps = DEP0CTL_MPS_64;
  hpcd_USB_FS.Init.phy_itface = PCD_PHY_EMBEDDED;
  hpcd_USB_FS.Init.low_power_enable = DISABLE;
  hpcd_USB_FS.Init.battery_charging_enable = DISABLE;
  HAL_PCD_Init(&hpcd_USB_FS);

}

/** Configure pins as
        * Analog
        * Input
        * Output
        * EVENT_OUT
        * EXTI
*/
void MX_GPIO_Init(void)
{

  /* GPIO Ports Clock Enable */
  __GPIOF_CLK_ENABLE();
  __GPIOA_CLK_ENABLE();
  __GPIOE_CLK_ENABLE();
  __GPIOB_CLK_ENABLE();
  __GPIOC_CLK_ENABLE();
  __GPIOD_CLK_ENABLE();

}

#ifdef USE_FULL_ASSERT

/**
   * @brief Reports the name of the source file and the source line number
   * where the assert_param error has occurred.
   * @param file: pointer to the source file name
   * @param line: assert_param error line source number
   * @retval None
   */
void assert_failed(uint8_t* file, uint32_t line)
{
  /* USER CODE BEGIN 6 */
  /* User can add his own implementation to report the file name and line number,
    ex: printf("Wrong parameters value: file %s on line %d\r\n", file, line) */
  /* USER CODE END 6 */

}

#endif

/**
  * @}
  */

/**
  * @}
*/

/************************ (C) COPYRIGHT STMicroelectronics *****END OF FILE****/

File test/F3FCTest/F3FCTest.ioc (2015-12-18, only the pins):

Mcu.UserName=STM32F303VCTx
PA11.Signal=USB_DM
PA12.Signal=USB_DP
PA13.Signal=SYS_JTMS-SWDIO
PA14.Signal=SYS_JTCK-SWCLK
PA2.Signal=USART2_TX
PA3.Signal=USART2_RX
PB10.Signal=USART3_TX
PC10.Signal=UART4_TX
PC11.Signal=UART4_RX
PC12.Signal=UART5_TX
PC13.Signal=GPIO_Output
PC14-OSC32_IN.Signal=GPIO_Output
PC15-OSC32_OUT.Signal=GPIO_Output
PD2.Signal=UART5_RX
PE15.Signal=USART3_RX
PF0-OSC_IN.Signal=RCC_OSC_IN
PF1-OSC_OUT.Signal=RCC_OSC_OUT

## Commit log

2015-11-08 v1 of the f3 flight controller
    [FlightController.drl, FlightController.gbl, FlightController.gbo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]
2015-11-10 v1 of f3fc
    [Bill_Of_Materials.csv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]
2015-11-10 v2 of the f3fc which adds pull up resistors for the i2c lines.
    [Bill_Of_Materials.csv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]
2015-11-25 v3 of f3fc. Correct mosfet pinout. Add measurement points. Remove MPU. Tweaked pinout with one less SPI.
    [Bill_Of_Materials.csv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]
2015-12-18 Initial blinky for f3fc. Compiles but not tested on the board.
2016-01-07 Move decoupling caps to the front side of the board, re-add the MPU and switch from a crystal to a resonator.
    [FlightController-B.Cu.gbl, FlightController-B.Mask.gbs, FlightController-B.Paste.gbp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]
2016-01-11 v4 of F3FC including stacking height label
    [Bill_Of_Materials.csv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]
2016-02-02 v5 of F3FC. Adjusts motor output location, switches to MPU-6000 and adds chickadee logo back.
    [Bill_Of_Materials.csv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]
2016-03-05 F3FC v6 which features correct reset circuitry.
    Also:
    * Routes USB as differential pair.
    * Corrects reset circuit.
    * Adds fiducials
    * Matches up LED numbering to reference
    * Supports current pin from power connector.
    [Bill_Of_Materials.csv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]
2016-04-07 More changes to F3. Can't remember what.
    [FlightController-B.Cu.gbl, FlightController-B.Mask.gbs, FlightController-B.Paste.gbp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]
2016-04-13 Rebrand everything to Polystack and increment versions.
    [FlightController.kicad_pcb]
2016-04-16 Final gerbers for test manufacturing run.
    [Bill_Of_Materials.csv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]
2016-06-07 Update polystack logo to bold variant and bump version number.
    [FlightController.kicad_pcb, FlightController.sch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]
2016-07-07 Add license information to many files. PCB design files are CC-BY and code is MIT license.
    [FlightController.kicad_pcb, FlightController.sch, Power.sch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]
2016-07-07 Convert to relative component and footprint paths.
    [FlightController.sch, Power.sch, Reset.sch]

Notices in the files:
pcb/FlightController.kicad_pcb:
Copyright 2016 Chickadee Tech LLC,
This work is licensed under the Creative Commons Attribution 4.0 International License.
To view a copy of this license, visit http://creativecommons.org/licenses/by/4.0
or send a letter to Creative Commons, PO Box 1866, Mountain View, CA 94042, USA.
